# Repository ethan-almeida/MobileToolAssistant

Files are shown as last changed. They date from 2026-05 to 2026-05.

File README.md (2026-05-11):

# Mobile Tool Assistant

An autonomous mobile robot that follows a worker and carries tools in indoor industrial environments.

# Tools Used

## Hardware
- STM32F407DISCO Development Board
- ESP8266MOD Microcontroller (Remote node)
- 2x DWM1000 UWB Modules (User tracking)
- 3x VL53L1X ToF Sensors (Obstacle detection)
- L298N Motor Driver
- 2x TT DC Gear Motors
- Buck Converter Module
- Rechargeable AA NiMH Batteries (8x)
- BambuLab P1S 3D Printer (Chassis)
- Multimeter, Soldering Iron, Jumper Wires, Protoboard

## Software
- STM32CubeIDE v1.19.0
- Arduino IDE v2.3.7
- FreeRTOS (Real-time OS on STM32)
- Serial Debug Assistant
- GitHub (Version control)

## Repository Structure
```
MobileToolAssistant
├── DWM1000_tests/ # Iterative UWB development tests 
├── MobileToolAssistant/ # Final source code
│ ├── RemoteEnd/ # User remote node (ESP8266)
│ └── RobotEnd/ # Robot platform (STM32)
├── docs/ # Documentation and CAD files
└── README.md
```

## Quick Start

1. **Hardware setup**: See [User Manual](./docs/user_manual.pdf) for assembly, battery installation, and power-on steps.
2. **Build & flash**:
   - Robot: STM32CubeIDE project in `MobileToolAssistant/RobotEnd/`
   - Remote: Arduino IDE sketch in `MobileToolAssistant/RemoteEnd/`
3. **Operation**: Press the STANDBY button on the remote to start/stop following.

## Key Features

- UWB‑based user tracking (1m ± 0.5m following distance)
- ToF obstacle detection and avoidance
- Remote standby control
- Payload capacity: 1 kg
- Max following speed: 6 km/h

## Overall Block Diagram 
 

## Documentation

- [Requirements Specification](./docs/appendices/requirements_specification.pdf)
- [System Specification](./docs/appendices/system_specification.pdf)
- [Project Management](./docs/appendices/project_management.pdf)
- [User Manual](./docs/appendices/user_manual.pdf)
- [Final Report](./docs/final_report.pdf)

## Team

- Aneek Mohamed Ruksan
- Aditya Ramakrishnan
- Ethan D'Almeida
- Chidubem Emeka-Nwuba

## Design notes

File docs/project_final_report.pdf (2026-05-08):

DEPARTMENT OF ELECTRICAL AND COMPUTER ENGINEERING UNIVERSITY OF SASKATCHEWAN
ECE495-2025G5 | VERSION 1 | MOBILE TOOL ASSISTANT

© 2025 Chidubem Emeka-Nwuba, Aneek Mohamed Ruksan, Aditya Ramakrishnan, Ethan D’Almeida.
This document is CONFIDENTIAL and PROPRIETARY and is for the use of University of Saskatchewan personnel only, except to the extent that permission is expressly granted elsewhere.

In any event, no part of this document may be reproduced in any form without the express written consent of University of Saskatchewan.

UNIVERSITY OF SASKATCHEWAN. PROPRIETARY AND CONFIDENTIAL | Page 1 of 28
DOC NO: | ECE495-2025G5 | ISSUE DATE: | 07-04-2026
FILE NAME: | G5_assign7_final_report.pdf | VERSION NO: | 1
FILING PATH: | https://github.com/AneekMubarak/MobileToolAssistant/blob/main/docs/
TITLE: | Final Project Report
PROJECT: | Mobile Tool Assistant
KEYWORDS: | Report, schedule, objectives, constraints, testing

APPROVED BY

Daniel Teng | Date
Customer

PREPARED BY:

Aditya Ramakrishnan Date
Design Engineer

Aneek Mohamed Ruksan Date
Design Engineer

Chidubem Emeka-Nwuba Date
Design Engineer
Ethan D’Almeida | Date
Design Engineer

REVIEWED BY:

Chandler Janzen | Date
Supervisor

© 2025 Chidubem Emeka-Nwuba, Aneek Mohamed Ruksan, Aditya Ramakrishnan, Ethan D’Almeida.
This document is CONFIDENTIAL and PROPRIETARY and is for the use of University of Saskatchewan personnel only, except to the extent that permission is expressly granted elsewhere.

In any event, no part of this document may be reproduced in any form without the express written consent of University of Saskatchewan.

UNIVERSITY OF SASKATCHEWAN. PROPRIETARY AND CONFIDENTIAL | Page 2 of 28

REVISION HISTORY
Version No. | Date | Originator | Summary of Changes
1 | 29-03-2026 | E.D | Document created

## Table of Contents

## List of Tables

Table 1: Testing Setups and Results | 22
Table 2: Expected Project Schedule | 23
Table 3: Actual Project Schedule | 24
Table 4: Individual Member Contribution Summary | 25

## List of Figures

Figure 1: Final System Block Diagram | 9
Figure 2: Detailed Design - Motor Control Subsystem | 12
Figure 3:Detailed Design - Obstacle Detection Subsystem | 13
Figure 4: Detailed Design - User Detection: Robot Node | 21
Figure 5: Detailed Design - User Detection: Remote Node | 21
Figure 6: Gantt Chart for Expected and Actual Project Schedule | 24

## Executive Summary

This project presents the design and implementation of the Mobile Tool Assistant, a proof-of-concept robotic system developed to reduce the physical strain associated with transporting tools in industrial environments. Existing solutions such as carts and tool belts either require continuous manual effort or place excessive load on workers, creating safety and ergonomic concerns.
To address this problem, our team developed an autonomous, user-following robot capable of carrying tools while navigating indoor environments. The system integrates Ultra-Wideband (UWB) technology for accurate user tracking and Time-of-Flight (ToF) sensors for real-time obstacle detection and avoidance. A central STM32 microcontroller coordinates all subsystems, including motion control, navigation, and power management, enabling reliable and responsive operation. The prototype successfully demonstrates key functionalities, including maintaining a safe following distance, navigating around obstacles, and supporting remote user control. Testing results show consistent performance in tracking users at walking speeds and avoiding collisions, though payload capacity and motor performance were identified as limiting factors.
Despite challenges such as UWB calibration complexity and system integration delays, the project achieved its primary objective of delivering a functional and cost-effective mobile assistant. The modular design allows for future improvements, including enhanced sensing coverage, more robust hardware integration, and upgraded power systems.
Overall, this work demonstrates the feasibility of an affordable robotic assistant that can improve workplace safety, reduce fatigue, and enhance productivity in demanding environments.

## Statement of Work

### Problem Description

The project addresses the physical strain of manually transporting tools and equipment in harsh work environments where affordable and accessible transport systems are lacking. The goal is to develop a mobile robotic assistant that can detect a worker, map a route, and follow them to carry tools safely and cost-effectively.

### Problem Background

Most workers who work in demanding or harsh environments, i.e. industries or factories, often must carry heavy tools on their person. This becomes an issue especially in industrial environments where operators cannot afford to have excess weight on them, causing safety hazards.
While current methods attempt to address this challenge, they fall short in practice. Workers often rely on push carts, dollies, hand trolleys, and rolling toolboxes to move heavy equipment. These require constant pushing or pulling and can be difficult to maneuver on uneven surfaces or in tight spaces. Other solutions include using a portable tool belt or backpacks. These keep tools within reach but place the full weight directly on the worker’s body, increasing fatigue and risk of injury over long shifts.
This forms a need to make a mobile, autonomous, and tool-carrying system that can follow a worker, transport equipment safely, and reduce physical strain without requiring continuous manual operation.

### Scope

The project will demonstrate a working proof-of-concept of a mobile tool assistant. The team will design, build, and test a small-scale robotic platform that can autonomously follow a single worker and carry a payload of tools across a flat or moderately uneven indoor surface. The work will involve selecting and assembling appropriate hardware such as motors, sensors, a supporting frame, and a battery to create a safe and stable prototype. On the software side, the team will implement core functions such as person-tracking, obstacle avoidance so that the robot can reliably follow a worker in a controlled environment. A user remote will also be developed to allow a worker to toggle between following and standby modes of the robot without requiring constant supervision.

### Objectives

The project team shall:
1. Develop and deliver proof of concept of a mobile prototype of a compact and safe robot capable of transporting small tool loads in an indoor industrial environment.
2. Implement a reliable person-following capability that allows the robot to detect and follow a designated worker after activation.
3. Integrate obstacle detection and avoidance to minimize collision risk in a dynamic workspace.

4. Demonstrate usability and safety by producing a working prototype within one academic year and within the approved budget.

### Constraints

The following constraints shall limit the design and implementation:

1. Single-Floor Navigation: The system shall be restricted to operation on flat, single-level surfaces with little to no debris. The design shall not support stair climbing or traversal of steep inclines.
2. Indoor Use: The system shall be designed for operation in indoor environments only. Outdoor operation is excluded due to environmental complexity and weatherproofing requirements.
3. Payload Capacity: The system shall be capable of carrying a moderate tool payload only, as limited by motor performance, chassis strength, and available project resources.
4. Timeframe: The project shall be executed within the academic year, which constrains the scope to the development of core functionalities rather than advanced features.
5. Team Size: The project shall be executed by a team of four members. The limited manpower constrains the project scope, task allocation, and development capacity within the given timeframe.
6. Budget: The project shall operate under limited financial resources, restricting the use of high-cost sensors, materials, and hardware.

### Key Considerations

The robotic assistant shall operate safely and non-distractingly, maintaining an appropriate distance from workers and functioning predictably to avoid interfering with normal workflows. The design should incorporate reliable load management, robust battery management, and durable, energy-efficient components to meet safety and operational requirements. The project should also emphasize positive social impact by reducing physical strain on workers, ensuring ease of use and accessibility, and reinforcing the role of the robot as an assistant that supports productivity rather than replacing human labor.

## Final System Block Diagram

The final system architecture of the Mobile Tool Assistant is designed as a modular, real-time embedded system that integrates user tracking, obstacle detection, motion control, and power management into a cohesive autonomous platform. The system enables the robot to follow a designated user while safely navigating indoor environments.

At a high level, the system consists of six primary subsystems: User Tracking, Navigation (Obstacle Detection), Motion Control, Processing and Communication, Power Management, and User Interface, all coordinated by a central microcontroller.

The User Tracking subsystem utilizes Ultra-Wideband (UWB) technology to estimate the relative position of the user. Two UWB anchors mounted on the robot perform ranging with a remote UWB node carried by the user. Using these distance measurements, the system computes the user’s position and heading relative to the robot.

The Navigation subsystem consists of multiple Time-of-Flight (ToF) sensors that continuously monitor the environment for obstacles. These sensors provide distance measurements that are used to detect potential collisions and trigger avoidance maneuvers.

The Motion Control subsystem translates tracking and navigation data into motor commands. It implements control logic to maintain a safe following distance while dynamically adjusting speed and direction. Obstacle avoidance is handled using a state-machine-based approach to ensure predictable and stable behavior.

The Processing and Communication subsystem is implemented on an STM32 microcontroller and acts as the core of the system. It handles sensor data acquisition, UWB communication, decision-making, and coordination between subsystems in real time.

The Power Management subsystem distributes power from a single battery source to all components. It includes voltage regulation for logic-level electronics and direct supply for motors, ensuring stable and efficient operation.

Finally, the User Interface subsystem allows the user to interact with the robot through a remote node and onboard controls. It enables start/stop functionality and provides basic system feedback.

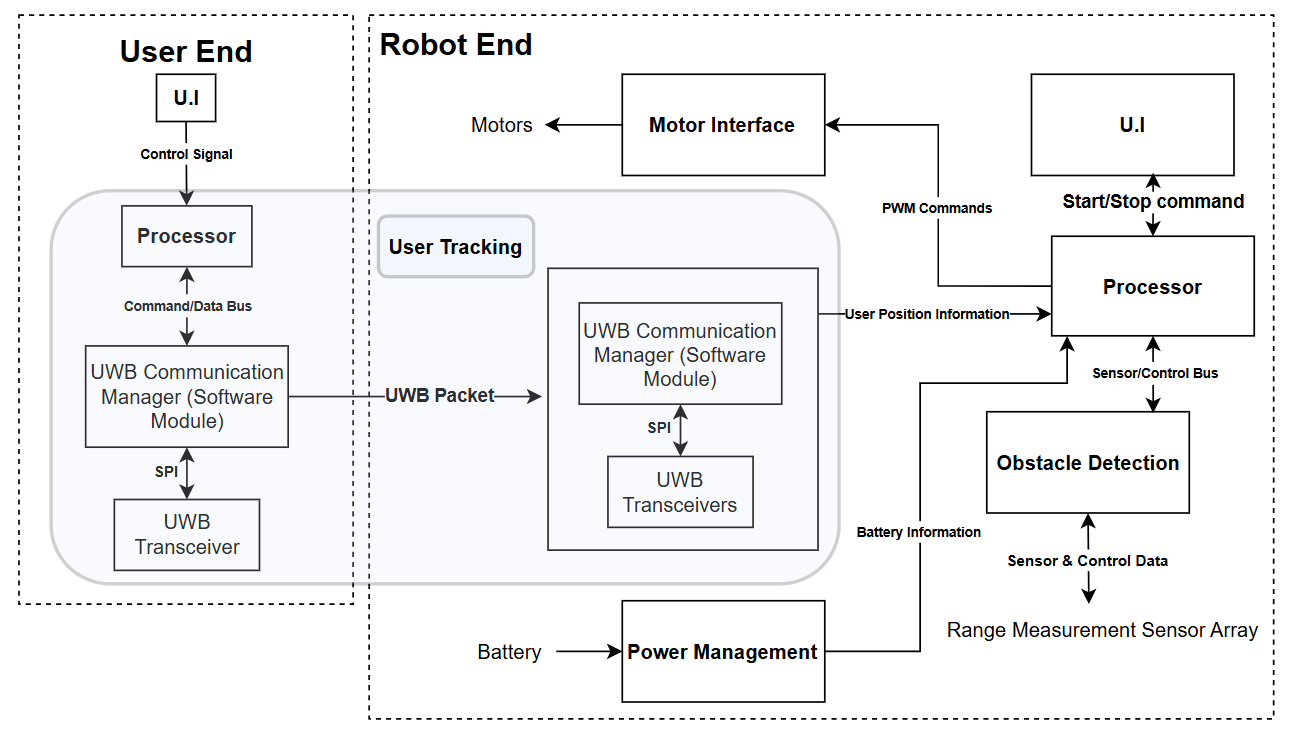
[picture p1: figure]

Figure 1: Final System Block Diagram

### System Alternatives and Design Selection

Several system architectures were considered during the design phase, including:
- Vision-based tracking with LiDAR navigation
- BLE-based tracking with RSSI and stereo vision
- BLE with IMU-assisted tracking
- UWB-based tracking (final design)
Each alternative was evaluated based on cost, complexity, power consumption, reliability, and implementation feasibility. Vision-based systems offered high accuracy but were computationally expensive and sensitive to lighting conditions. BLE-based approaches were low-cost but suffered from poor positional accuracy due to signal variability.
The UWB-based system was selected as the final design because it provides high-accuracy distance measurements, low latency, and robustness in indoor environments, while remaining within project cost and power constraints. This made it the most balanced and practical solution for a real-time following system.

### Key Design Decisions

Several important design decisions were made to ensure system performance and feasibility:
- Use of dual UWB anchors: Enabled triangulation of user position rather than relying on a single distance measurement, improving tracking accuracy.
- RTOS-based control architecture: Simplified implementation of all subsystems and ensured predictable system behavior.

- Modular subsystem design: Allowed independent development and testing of tracking, control, and sensing components.
- Use of ToF sensors over LiDAR: Reduced system cost and power consumption while still meeting obstacle detection requirements.
- Single battery power architecture: Simplified integration and reduced hardware complexity.

### Design Challenges and Solutions

Several challenges were encountered during system development:
- UWB calibration and instability:
Achieving accurate distance measurements required careful calibration of antenna delays and filtering of noisy readings. This was addressed through averaging multiple samples and iterative calibration.
- Integration of multiple subsystems:
Synchronizing tracking, obstacle detection, and motion control introduced timing and communication challenges. These were mitigated by implementing structured state machines and prioritizing obstacle avoidance over tracking.
- Limited field of view for tracking:
The use of two front-mounted UWB anchors restricted tracking to a forward-facing region. This limitation was accepted for the prototype but identified for future improvement.
- Motor performance under load:
The robot experienced reduced performance with higher payloads. This was partially mitigated through speed control adjustments and is noted as a limitation of the prototype hardware.

## Final Detailed Design

(A – Aditya Ramakrishnan, B – Aneek Mohamed Ruksan, C –Chidubem Emeka-Nwuba, D – Ethan Peter D’Almeida)

### Processor (A: 90% C: 10%)

Purpose:
The Processor Module reads all sensor inputs, determines the robot’s motion commands, and sends control signals to the motor drivers. It handles UWB ranging, battery monitoring, state decisions, and safety shutdown actions at the robot’s end.
Inputs:
- UWB Positional Data & Start/Hold Commands
- ToF Sensor Obstacle Detection Distance Data array
- Battery Voltage/Current
Outputs:
- 4× PWM Motor Signals
- UWB Configuration Commands

Parts Required:
- STM32F407DISC0 Development Board
- STM32CubeIDE

### Motor Control (D: 100%)

Purpose:
The motion control subsystem is responsible for converting the user’s position from the User Tracking subsystem into motor drive signals.
Inputs:
- User Position (x, y) from User Tracking subsystem.
- System State (from obstacle detector and from UI) Parts Required:
- 2x TT Gear Motor
- 1x L298N Driver
Algorithm:
- Read raw ToF distances from the left, center, and right sensors.
- If in “STANDBY_MODE”, immediately stop motors and reset the obstacle state machine.
- Obstacle avoidance is handled by a 3-phase state machine
- The states are: - OBST_STATE_STOP_BEFORE, OBST_STATE_ACTION, OBST_STATE_STOP_AFTER
- Motor Control Logic:
- If center < OBSTACLE_THRESHOLD_CLOSE, then the reverse command is given, dodgeAngle is set to 180 degrees, and the state machine is initiated.
- If center_blocked is true, then the robot will turn towards the side with more clearance, i.e., turn left by 135 degrees and turn right by 45 degrees.
- If left_blocked then turn right at 45 degrees.
- If right_blocked then turn left at 135 degrees.
- If both sides are blocked but the center is clear, move forward at constant speed and maintain a dodgeAngle of 90 degrees.
- UWB Following Logic:
- If the distance from the remote to the robot is within the range of 0.25 m to 30 m, the angle is within a range of 0 to 180 degrees, and the valid flag is set, then the UWB data will be accepted.
- The robot will stop if the distance to the remote is less than or equal to 100 cm and will only resume when that distance becomes greater than 115 cm (tolerance measure).
- Speed Control Logic:

- The PWM signal is adjusted by the distance from the remote to the robot, i.e., a smaller distance results in a lower speed, and a higher distance results in a higher speed.

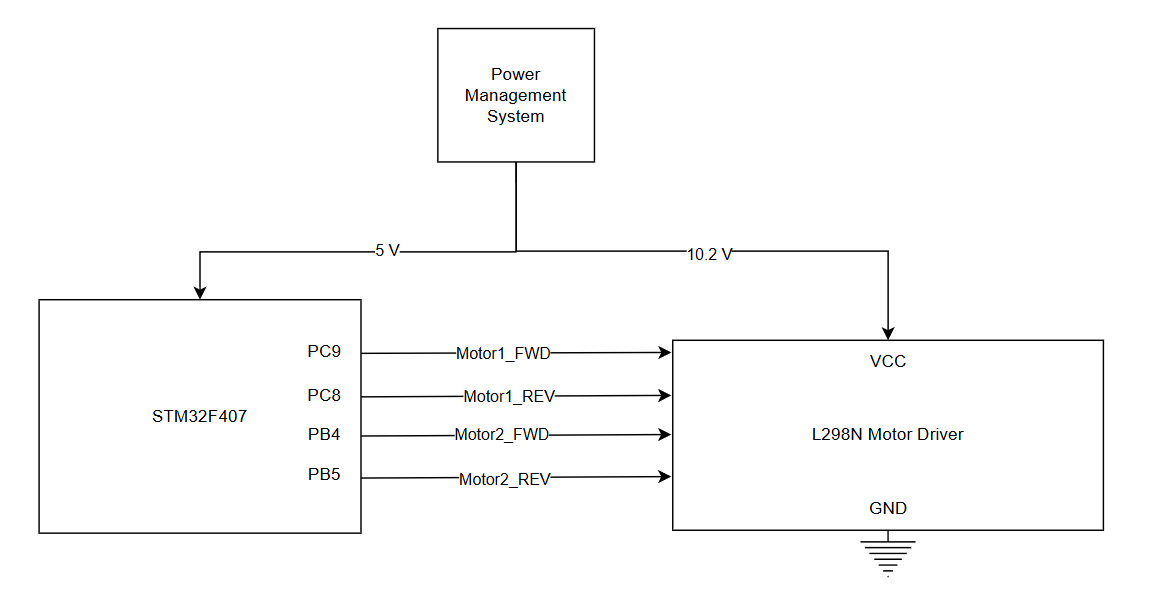
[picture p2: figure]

Figure 2: Detailed Design - Motor Control Subsystem

### Obstacle Detection (C: 90%, A: 10%)

Purpose:
The purpose of the Obstacle Detection subsystem is to detect obstacles in the robot’s path from a minimum distance of 1.5m. This information is then sent to the microcontroller to process and make decisions on whether to keep following the user or avoid an incoming obstacle. The decision is made based on the sensor data stored in a data array for each sensor. The sensors used are 3 VL53L1X placed to provide coverage to the front-facing side of the robot (Refer to Figure 3 for wiring/connection specifications).
Outputs:
Obstacle detection distances from each ToF sensor
Software Algorithm:
- Monitors surroundings using left, center, and right ToF sensors with filtered distance readings
- Determines whether paths are blocked based on distance thresholds (center and side zones)
- Prioritizes obstacle avoidance over normal movement and pauses user-following when needed

- Executes avoidance maneuvers through a state machine to complete multi-step actions reliably
- Reverses immediately when an obstacle is detected very close in front
- Chooses a turn direction (left or right) based on which side has more clearance
- Turns away from obstacles detected on only one side
- Continue moving forward when only side paths are blocked, but the center is clear
- Adjusts its dodge angle to guide the direction of avoidance maneuvers
- Resumes normal user-following behavior when no obstacles are detected

Parts Required:
1. 3 VL53L1X sensors
2. Protoboard to solder buses together
3. Jumper wires (to connect to MCU)

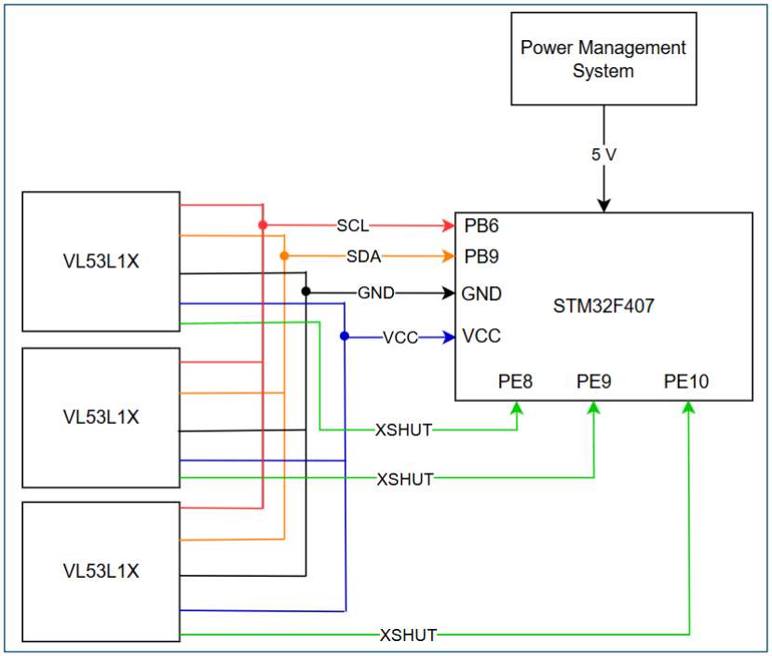
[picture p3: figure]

Figure 3:Detailed Design - Obstacle Detection Subsystem

### Power Management (A: 100%)

Purpose:
The Power Management Module provides the required voltage for the robot from an 8-cell rechargeable AA battery pack connected in series. The battery pack supplies power directly to the motor driver and feeds a buck converter that steps the voltage down to 5 V for the STM32F407 board. The board then powers and interfaces with UWB modules and distance sensors. This allows the robot to use a single battery source for both motor actuation and control electronics.

Output:
- Approximately 9.6 V nominal battery supply to motor driver
- Approximately 10.2 V when fully charged at startup
- 5 V rail to STM32F407 board through buck converter
- Power to 2× UWB modules through the board
- Power to 3× distance sensors through the board

Parts Required:
- 8 × Energizer rechargeable NiMH AA batteries (1.2 V each)
- 1 × battery holder/connector
- 1 × motor driver
- 1 × buck converter
- 1 × STM32F407 board
- 2 × UWB modules
- 3 × distance sensors
- 2 × yellow DC motors

Power setup:
- Connect the 8 AA rechargeable batteries in series to create the main supply voltage.
- Provide this battery voltage directly to the motor driver to power the motors.
- Feed the same battery voltage into the buck converter.
- Step the battery voltage down to a regulated 5 V output.
- Supply the 5 V output to the STM32F407 board.
- Use the STM32F407 board to power and interface with UWB modules and distance sensors.
- Continue operation while the battery pack provides supicient voltage.

Power Calculation:

Battery Pack Voltage
Nominal Voltage (V) = 8 ∗ 1.2V = 9.6V Fully charged (measured):
V ≈ 10.2 V
Motor Power (2 DC Yellow Motors) = ~10 V / ~0.25 A eacℎ (under load)

Rated electrical power per motor: P = 10 V × 0.25 A = 2.5 W

Total motor power:
P_total = 2 × 2.5 W = 5.0 W STM32F407 Development Board Power − 5 V / ~0.15 A P = 5 V × 0.15 A = 0.75 W
UWB Modules (2 × DWM1000) − 3.3 V / ~0.16 A eacℎ

Total current:
I = 2 × 0.16 A = 0.32 A

Total UWB power:
P = 3.3 V × 0.32 A = 1.056 W Distance Sensors (3 × ToF) − 5 V / ~0.02 A eacℎ

Total current:
I = 3 × 0.02 A = 0.06 A

Total sensor power:
P = 5 V × 0.06 A = 0.30 W

Total Average Power:
P_total = 5.0 W + 0.75 W + 1.056 W + 0.30 W P_total = 7.106 W

### User Tracking (B:100%)

Purpose:
The User Tracking subsystem determines the position of the user relative to the front of the robot so that the motion controller can steer toward the user and maintain the desired following distance. The implemented design uses two front-mounted UWB anchors on the robot and one UWB transceiver on the remote carried by the user. Distances from the left and right robot anchors to the remote are measured using Double-Sided Two-Way Ranging (DS-TWR), then converted into user position, distance, and heading angle.

Physical Setup:
The robot node uses two DWM1000 UWB modules mounted at the front of the robot on a rigid horizontal arm. The modules are placed 30 cm apart, centered about the robot midpoint, so that the left anchor is at −15 cm and the right anchor is at +15 cm relative to the robot centerline. This baseline is used directly in the triangulation calculation. The arm is mounted parallel to the front edge of the robot chassis so that both modules face forward and remain fixed relative to one another. The robot-side processing runs on the STM32F407 board as part of the RTOS application. The remote node carried by the user contains one DWM1000 module, one ESP8266MOD, and one pushbutton. The push button is used to transmit a standby control message to the robot. On the robot side, receipt of this message toggles the standby state used by the rest of the system. Inputs:
- UWB ranging frames received from the remote node
- Standby command embedded in remote UWB communication
Outputs:
- User position relative to robot center, (x, y), in cm
- User distance from robot center in cm
- User heading angle in degrees
- Standby state flag for higher-level control logic

Parts Required:
Robot Node:
1. STM32F407 development board
2. 2 x DWM1000 UWB Modules
3. 1 x rigid front mounting arm for the anchors (30cm)
4. Wiring for SPI, reset, interrupt and power connections

Remote Node:
1. ESP8266MOD Microcontroller
2. 1 x DWM1000 Module
3. 1 x Pushbutton for standby control
4. Portable power source for the remote node (5V).

System Operation:
The robot does not estimate position from a single UWB reading. Instead, it ranges separately to the left and right front anchors and then computes the user’s position geometrically. For each anchor, the ranging exchange is performed using DS-TWR. In one ranging cycle, the robot sends a Poll frame, the remote replies with a Response frame, the robot sends a second Poll 2 frame, and the remote replies with a Final frame. Timestamps recorded on both sides are used to compute the signal propagation time while compensating for reply delays. The propagation time is converted to distance, corrected using antenna-delay compensation.

The DS-TWR propagation time is calculated as: t!"#! = (rtt$. rtt%) − (reply$. reply%) rtt$ + rtt% + reply$ + reply% Where:
- t!"#!: Signal propagation time between the robot and the remote node
- rtt$: Round-trip time measured during the first message exchange (Poll to Response)
- rtt%: Round-trip time measured during the second message exchange (Poll2 to Final)
- reply$: Reply delay at the remote node (time between receiving Poll and sending Response)
- reply%: Reply delay at the robot (time between receiving Response and sending Poll 2)

The measured distance (d) is then computed from:
d = t!"#!. c
Where c is the speed of light. In the implementation, antenna delay is subtracted before the time is converted to distance.
To reduce noise, the robot averages multiple distance measurements from the left and right anchors before computing the user position. The code uses an averaging count of 5 samples. After valid left and right distances are available, the position is calculated using the fixed baseline between the anchors
Coordinate System:
The coordinate system is defined with the robot center at the origin. Positive x points to the robot’s right side, and positive y points forward. With the anchor baseline B = 30cm, the left anchor is located at (−15,0)and the right anchor is located at (+15,0). The user position is calculated from the left and right distances d&and d'as:
x = d&

% − d'

%
2B
y = ](d&
% − ^x +

B
2

_

%

The user's distance from the robot center is then: d = `x% + y%
The user heading angle is computed from:
θ = atan2(y, x)
In this convention, 0° is directly to the right of the robot, 90° is straight ahead, and 180° is directly to the left.
Standby Control:
The remote node also transmits a control message used to toggle standby mode. On the robot side, if the received message type is identified as a standby frame, the standby flag is toggled. This allows the user to command the robot to pause or resume tracking using the push button on the remote.
UWB Configuration Parameters:
The DWM1000 modules on both the robot and remote nodes are configured using a fixed set of communication parameters to ensure consistent ranging performance. The following configuration is used for all UWB devices in the system:
- Channel: 5
- Pulse Repetition Frequency (PRF): 16 MHz
- Data Rate: 6.8 Mbps
- Preamble Length: 1024 symbols
- PAC Size: 32
- SFD: Standard
- Antenna Delay: Calibrated per module
Channel 5 and a data rate of 6.8 Mbps were selected to achieve reliable communication with low latency and sufficient range (~30 m) for the intended indoor tracking environment.
All nodes must use identical configuration parameters to ensure successful communication and accurate ranging.
SPI Communication Configuration:
The SPI interface used to communicate with the DWM1000 modules is initialized at a lower clock frequency during startup and configuration, then increased for normal operation. Initialization Phase SPI Speed: Remote node - 3 MHz; Robot node - 328.125 kHz
Operational Phase SPI Speed: Remote node - 20 MHz; Robot node - 10.5 MHz
UWB Message Structure:
To distinguish between different stages of the DS-TWR protocol and control messages, a custom message format is used for all UWB transmissions.

Each transmitted frame contains a fixed 6-byte payload. The most significant byte (MSB) of the payload represents the message type, while the remaining 5 bytes (lower 40 bits) are used to store timing-related values such as timestamps or reply delays required for DS-TWR calculations.

The following message types are defined:
- 0xA1 – POLL
- 0xB2 – RESPONSE
- 0xA2 – POLL_2
- 0xA3 – FINAL
- 0x69 – STANDBY CONTROL
During operation, the receiving node inspects the message type field to determine the appropriate state transition and processing logic.

In addition to the message type, RESPONSE and FINAL frames include embedded timing information required for DS-TWR calculations, such as reply delays and timestamps.

This structured message format ensures correct synchronization between the robot and remote nodes and enables reliable execution of the ranging protocol and standby control.
Algorithm:
The User Tracking subsystem is implemented using finite state machines on both the robot node and the remote node. The robot state machine manages the DS-TWR ranging process and distance computation, while the remote state machine handles message responses and control transmission. Each state represents a specific stage in the ranging protocol, ensuring reliable communication, timing control, and error recovery.
Robot State Machine States:
- RSTATE_SEND_POLL
- RSTATE_WAIT_RESPONSE_1
- RSTATE_SEND_POLL_2
- RSTATE_WAIT_RESPONSE_2
- RSTATE_COMPUTE
- RSTATE_ERROR_RECOVERY

Remote State Machine States:
- REMOTE_WAIT_M1
- REMOTE_SEND_M2
- REMOTE_WAIT_TX_DONE
- REMOTE_WAIT_M3
- REMOTE_SEND_M4
- REMOTE_WAIT_TX_DONE_FINAL

The following algorithm describes the real-time execution of the state machines on both robot and remote nodes.
1. Initialize SPI, reset, and interrupt interfaces and apply the predefined UWB configuration parameters.
2. Set the robot ranging state to RSTATE_SEND_POLL for the active anchor and set the remote state to REMOTE_WAIT_M1.
3. For the active robot anchor, transmit a POLL frame to the remote node.
4. On the remote node, wait in REMOTE_WAIT_M1 until a valid POLL frame is received. If the received frame is invalid or a timeout occurs, clear status flags, reset the remote session, and return to REMOTE_WAIT_M1.
5. After receiving a valid POLL frame, the remote records the reception timestamp, computes the reply delay, and enters REMOTE_SEND_M2. It then transmits a delayed RESPONSE frame containing the reply timing information and moves to REMOTE_WAIT_TX_DONE.
6. The robot waits in RSTATE_WAIT_RESPONSE_1 for the Response frame. If the frame is invalid or a timeout occurs, the robot enters RSTATE_ERROR_RECOVERY, clears the transceiver state, and restarts the ranging sequence for that anchor.
7. After a valid RESPONSE frame is received, the robot stores the received timing data, transmits a second POLL_2 frame, and enters RSTATE_WAIT_RESPONSE_2.

8. On the remote node, once transmission of the RESPONSE frame is complete, the state machine moves to REMOTE_WAIT_M3. The remote waits for a valid POLL_2 frame. If reception fails or the wrong message type is received, the remote resets its session and returns to REMOTE_WAIT_M1.
9. After receiving POLL_2, the remote records the second reception timestamp, computes the second delayed reply, enters REMOTE_SEND_M4, and transmits the FINAL frame. It then waits in REMOTE_WAIT_TX_DONE_FINAL and, after successful transmission, returns to REMOTE_WAIT_M1.
10. The robot receives the FINAL frame in RSTATE_WAIT_RESPONSE_2. Using the stored timestamps and reply values, it computes the DS-TWR propagation time, applies antenna-delay compensation, and converts the result to distance for the active anchor. It then enters RSTATE_COMPUTE.
11. If the computed distance is valid, store it in the averaging buper for that anchor. If the measurement is invalid, discard it and restart the ranging sequence.
12. Repeat the ranging process for both left and right anchors to obtain one valid distance measurement from each.
13. Continue collecting measurements until the required number of valid samples is reached for both anchors. Average the left and right distances using the configured sample count of 5 to reduce noise before position estimation.
14. Use the averaged left and right distances to compute the user position (x, y), total distance from the robot center, and heading angle relative to the front of the robot.
15. Check the received message type for a standby control message. If a standby frame is detected, toggle the standby flag so the robot pauses.
16. Output the updated user position, distance, angle, and standby state to be used by the motion control subsystem.
17. Repeat the full process continuously while the system is powered.

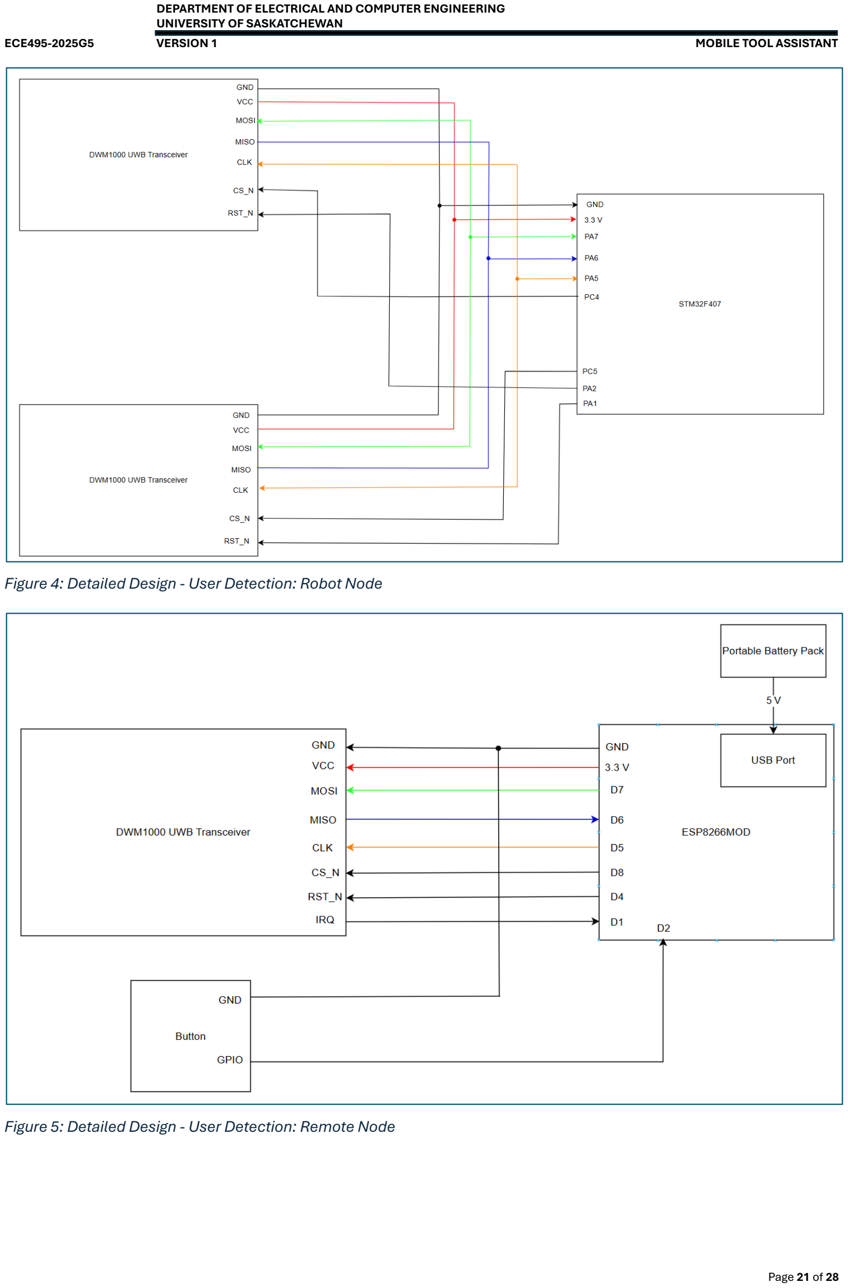
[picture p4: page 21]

Figure 4: Detailed Design - User Detection: Robot Node

Figure 5: Detailed Design - User Detection: Remote Node

## Development Environment

1. Hardware Used: -
- Multimeter
- Soldering Iron
- BambuLab P1S 3D printer
2. Software Used: -
- STM32Cube IDE v1.19.0
- Serial Debug Assistant
- Arduino IDE v2.3.7

## Testing Setups and Results

Table 1: Testing Setups and Results

Test ID | Requirement | Test Objective | Test Procedure | Expected Result | Actual Result
T1 | Follow distance: 1m ± 0.5 | Verify the robot maintains a proper following distance from the remote. | Place the robot at varying distances (0.5m to 2m) and measure the actual following distance | The robot should be able to maintain an average distance of 1m, ± 0.5m in all trials. | Robot maintains an average following distance of 1 ± 0.5 m in all the trials we conducted.
T2 | Follow speed: 5 km/h, ±1 km/h | Verify the robot’s ability to follow a moving user at a specified speed. | The user should move at speeds up to 5 km/h to measure the robot's following feature. | The robot should be able to track and follow a user in the environment it is operating in. | The robot was successfully able to track and follow the user at walking speeds of up to 6 km/h.
T3 | Payload: 5 kg capacity | Verify the robot’s ability to carry a payload safely. | Place a payload on the robot that weighs up to 5 kg and checks if it can follow the user in its operating environment. | The robot should be able to track and follow a user with a payload of up to 5kg in weight. | The robot was able to track and follow a user with a payload of up to 1kg without any issues. An increase in weight resulted in significant speed drops due to motor constraints.

T4 | Obstacle Detection

Verify the
robot’s ability
to detect and
avoid
obstacles.

Place static
obstacles
within 50 cm of
the robot’s
path.

The robot
should be able
to detect
obstacles
within 50 cm of
it and adjust its
path to
continue
tracking and
following the
user.

The robot was
able to
successfully
detect
obstacles
within 50 cm of
its path and
adjust its
course to
continue
following the
user.

## Actual v/s Expected Project Schedule

### Table 2: Expected Project Schedule

Task ID | Task Name | Estimated Hours | Responsible Member | Precedence | Expected Deadline
1 | Detailed Design (Assignment) | 20h | Chidubem | None | 27th Nov,2025.
2 | Parts Selection and Ordering | 10h | Aditya | T1 | 1st Dec,2025.
3 UWB Tracking Module (User | Tracking) | 40h | Aneek | T2 | 21st Jan, 2026.
4 | Obstacle Detection | 45h | Chidubem | T2 | 21st Jan, 2026.
5 Motion Control Algorithm (Motor | wiring) | 21h | Ethan | T3, T4 | 30th Jan, 2026
6 User Interface (and User Node | Assembly) | 20h | Aneek | T3 | 30th Jan, 2026
7 | Power Management System | 24h | Aditya | T1 | 21st Jan, 2026
8 System Assembly and Integration | (Constructing Prototype) | 30h | Chidubem | T5, T6, T7 | 15th Feb, 2026
9 Chassis Design and | Printing/Ordering | 15h | Aditya | T8 | 15th Feb, 2026
10 | System Testing and Debugging | 37h | Ethan | T9 | 28th Feb, 2026
11 System Refining and | Performance Improvement | 16h | Aneek | T10 | 28th Feb, 2026

### Table 3: Actual Project Schedule

Task ID | Task Name | Actual Hours Spent | Responsible Member | Precede nce | Completion Date
1 | Detailed Design (Assignment) | 20h | Chidubem | None | 27th Nov 2025.
2 | Parts Selection and Ordering | 25h | Aditya | T1 | 27th Jan 2026.
3 UWB Tracking Module (User | Tracking) | 175h | Aneek | T2 | 12th Mar 2026.
4 | Obstacle Detection | 45h | Chidubem | T2 | 4th Mar 2026.
5 Motion Control Algorithm (Motor | wiring) | 43h | Ethan | T3, T4 | 24th Mar 2026
6 User Interface and User Node | Assembly | 5h | Aneek | T3 | 13th Mar 2026
7 | Power Management System | 24h | Aditya | T1 | 20th Mar 2026
8 System Assembly and Integration | (Constructing Prototype) | 30h | Chidubem | T5, T6, T7 | 23rd Mar 2026
9 Chassis Design and | Printing/Ordering | 15h | Aditya | T8 | 19th Mar 2026
10 | System Testing and Debugging | 40h | Ethan | T9 | 24th Mar 2026
11 System Refining and | Performance Improvement | 37h | Aneek | T10 | 24th Mar 2026

Figure 6: Gantt Chart for Expected and Actual Project Schedule

Planned
Actual

Expected vs Actual Project Schedule

Legend

Task | November | December | January | February | March

Detailed Design

Part Selection and Ordering

UWB Tracking Module/User Tracking

Obstacle Detection

Motion Control Algorithm

User Interface (and User Node Assembly) !D#$%&'()(*$+$),&-./,$+

-./,$+&0//$+12.&()3&4),$*%(,5D)&67D)/,%89,5)*&!%D,D,.:$; 7<(//5/&=$/5*)&()3&!%5),5)*

-./,$+&>$/,5)*&()3&=$18**5)*&

-./,$+&?$@5)5)*&()3&!$%@D%+()9$&4+:%DA$+$),

### Table 4: Individual Member Contribution Summary

Member | Total Hours | Key Contributions
Aneek Mohamed Ruksan | 180 | UWB User Tracking, UI/User Node
Aditya Ramakrishnan | 120 | Motor Control Algorithm, Power Management System, Obstacle Avoidance, Chassis Design and Printing, System Refining and Improvement, System Assembly
Ethan D’Almeida | 70 | UWB calibration support and testing, documentation, obstacle detection, and avoidance improvements
Chidubem Emeka-Nwuba | 75 | Obstacle Detection Subsystem Assembly and Integration, Software architecture: implementation, management, and subsystem task integration

Project Analysis and Reflection
The project did not follow the original schedule mainly because some tasks were much more difficult than expected. The biggest issue was our lack of experience with UWB technology, which led to large delays early on the project and later affected many tasks. The largest difference was in the UWB tracking module (Task-3), which took us 175 hrs to complete and get fully working rather than the planned 40 hrs. Main challenges in this task that can be attributed to the delay include: -
- Calibrating the antenna delay, which required multiple rounds of testing and adjustments.
- Implementing the double-sided two-way ranging algorithm correctly.
- Fixing drift in tracking and unstable position and direction readings.

This task was required because it was the highlight feature of our project and had to be completed before others could start, which caused a chain reaction that pushed back multiple tasks, such as motion control and system integration.

Other tasks also took longer than expected, such as: -
- Parts Selection (Task-2): Took 25 hrs instead of 10 hrs due to re-designs and part availability.
- Motion Control (Task-5): Took 43 hrs instead of 21 hrs due to issues in integration.
- System Refinement (Task-11): Took 37 hrs instead of 16 hrs due to extra testing and improvements, specifically in the obstacle avoidance algorithm.
However, some time was saved in the User Interface (Task-6), which only took 5 hrs instead of 20 hrs because the design was simplified.

Mitigation Strategies

To deal with the delays, our team made some adjustments: -
- Ethan helped Aneek with UWB calibration and testing, which improved progress on one of the more dipicult tasks in the project.
- Some tasks, such as obstacle detection and the power management system, were done in parallel to reduce any further delays.
- Features like the user interface were greatly simplified to save time.
- Instead of waiting till the end, we tested parts of the system to catch any problems earlier.
- More time was spent on testing and refinement to ensure the system worked reliably.

## Recommendations

While the final system meets the core project requirements, it was developed as a proof-of-concept prototype with several design trade-offs that impact performance, reliability, and scalability. One key limitation was in the UWB tracking system, where the use of only two sensors provided a 180° field of view, constraining the user to remain in front of the robot; in the intended design, adding a third sensor at the rear would enable full 360° coverage and allow continuous tracking regardless of user position. Similarly, the prototype relied primarily on ToF sensors for obstacle detection, which limited environmental awareness; integrating a 360° LIDAR sensor in the final design would provide comprehensive planar coverage for navigation, while the existing ToF sensors could be retained for vertical distance measurement, resulting in improved obstacle detection and avoidance across a wider range of scenarios. Additionally, the use of jumper wire connections in the prototype, while beneficial for rapid development, introduced reliability issues such as loose connections, signal instability, and inconsistent test results; transitioning to custom PCBs in the intended design would significantly enhance electrical reliability, mechanical robustness, and signal integrity, while also simplifying assembly, reducing noise susceptibility, and enabling more accurate and repeatable system testing. Finally, future iterations will focus on improving the power system by transitioning to an industry-standard lithium-ion battery module, like those used in robotic vacuum platforms such as Roomba; this would involve a sealed, rechargeable battery pack with an integrated battery management system, enabling safer operation, higher energy density, and more reliable long-term performance.

## Conclusions

Our project successfully developed and tested a mobile robotic assistant, demonstrating a cost-effective solution for transporting heavy tools in demanding industrial environments. Our design integrates Ultra-Wideband (UWB) and Time-of-Flight (ToF) sensor technologies, providing a robust platform capable of autonomously tracking a worker while maintaining safe distances and navigating around dynamic obstacles. Furthermore, our implementation of a remote-based standby control system ensures the robot operates as an intuitive assistant that responds to user commands without requiring constant manual supervision.
The design relies on a modular architecture, utilizing a central STM32 microcontroller to process UWB ranging data and ToF obstacle inputs, which are then translated into precise motor commands. The UWB modules allow for reliable user localization via trilateration, while the ToF sensor array provides real-time environmental awareness, enabling the robot to navigate safely in tight, indoor workspaces. These components allowed our team to implement a functional proof-of-concept using a budget-conscious approach that prioritizes both safety and ease of use.
While further refinement is necessary, specifically regarding long-term signal stability and power system optimization, the prototype successfully proves the core concepts of autonomous person-following and obstacle avoidance. The development process has provided a clear roadmap for future iterations, including moving to custom PCB designs and higher-density battery solutions. Ultimately, this work contributes to the development of affordable, high-utility robotic assistants designed to reduce physical strain and increase productivity for workers in industrial and construction settings.

## References

Decawave Ltd. (2017). DW1000 product datasheet (Version 2.22) [Data sheet]. https://www.qorvo.com/products/p/DW1000

Decawave Ltd. (2017). DW1000 user manual (Version 2.18) [User manual]. https://www.qorvo.com/products/p/DW1000

Qorvo. (n.d.). DWM1000 ultra-wideband module (Version 2.0) [Data sheet]. https://www.qorvo.com/products/d/da007948

Amazon Web Services, Inc. (2017). FreeRTOS reference manual (Version 10.0.0) [Reference manual].
https://www.freertos.org/media/2018/FreeRTOS_Reference_Manual_V10.0.0.pdf

STMicroelectronics. (2024). VL53L1X time-of-flight ranging sensor (Rev. 8) [Data sheet]. https://www.st.com/resource/en/datasheet/vl53l1x.pdf

STMicroelectronics. (2026). STM32F407xx Development Board (Rev. 11) [Data sheet]. https://www.st.com/resource/en/datasheet/dm00037051.pdf

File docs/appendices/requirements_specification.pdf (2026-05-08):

DEPARTMENT OF ELECTRICAL AND COMPUTER ENGINEERING UNIVERSITY OF SASKATCHEWAN
ECE495-2025G502 | VERSION 0.2 | REQUIREMENT SPECIFICATION

© Chidubem Emeka-Nwuba, Aneek Mohamed Ruksan, Aditya Ramakrishnan, Ethan D’Almeida.

This document is CONFIDENTIAL and PROPRIETARY and is for the use of the copyright holders, except to the extent that permission is expressly granted elsewhere.

In any event, no part of this document may be reproduced in any form without the express written consent of the copyright holders.

UNIVERSITY OF SASKATCHEWAN. PROPRIETARY AND CONDIDENTIAL | Page 1 of 9
DOC NO: | ECE495-2025G502 | ISSUE DATE: | 07-10-2025
FILE NAME: | g5_assign2_requirements_specification.pdfVERSION NO: | 0.2
FILING PATH: | https://github.com/AneekMubarak/MobileToolAssistant/blob/main/docs/
TITLE: | Requirement Specification
PROJECT: | Mobile Tool Assistant
KEYWORDS: | tools, assistant, navigation, transport, follow, requirements, specifications, constraints,
| functional, non-functional.

APPROVED BY

Daniel Teng | Date
Customer

PREPARED BY:

Chidubem Emeka-Nwuba | Date
Design Engineer
Aditya Ramakrishnan | Date
Design Engineer
Aneek Mohamed Ruksan | Date
Design Engineer
Ethan D’Almeida | Date
Design Engineer

REVIEWED BY:

Chandler Janzen | Date
Supervisor

© Chidubem Emeka-Nwuba, Aneek Mohamed Ruksan, Aditya Ramakrishnan, Ethan D’Almeida.

This document is CONFIDENTIAL and PROPRIETARY and is for the use of the copyright holders, except to the extent that permission is expressly granted elsewhere.

In any event, no part of this document may be reproduced in any form without the express written consent of the copyright holders.

UNIVERSITY OF SASKATCHEWAN. PROPRIETARY AND CONDIDENTIAL | Page 2 of 9

REVISION HISTORY
Version No. | Date | Originator | Summary of Changes
1 | 07-10-2025 | C.E.N, A.R, E.D, A.M.R | Document Created
2 | 04-11-2024 | E.D | Modified Design Constraints, reframed some requirements
3 | 25-03-2026 | E.D | Updated Design Constraints, updated detection thresholds
4 | 07-04-2026 | C.E.N, A.R | Updated requirements, constraints and key requirements

© Chidubem Emeka-Nwuba, Aneek Mohamed Ruksan, Aditya Ramakrishnan, Ethan D’Almeida.

This document is CONFIDENTIAL and PROPRIETARY and is for the use of the copyright holders, except to the extent that permission is expressly granted elsewhere.

In any event, no part of this document may be reproduced in any form without the express written consent of the copyright holders.

UNIVERSITY OF SASKATCHEWAN. PROPRIETARY AND CONDIDENTIAL | Page 3 of 9

## Table of Contents

# Requirement Specification

This section outlines the functional and performance requirements of the system, detailing the design objectives, operational constraints, and expected behaviors necessary to ensure that the implementation meets its intended purpose.

## Functional Requirements:

The functional requirements for the design and implementation of this project are listed below: Functionality (ID: 01):
Type of Constraint | Requirement Description
Performance/Capability | The robot shall be able to follow the user within a 100 cm radius when not in standby.
Performance/Capability | The robot shall be able to follow the user at a speed of 5 km/h (±1km/h) when following a user.
Performance/Capability | The robot shall be able to carry a payload of up to 25 kg securely during operation.
Performance / Timeliness | The system shall be able to detect and avoid obstacles within 150 cm and reroute to continue following the user.

Hardware (ID: 02):
Type of Constraint | Requirement Description
Performance/Capacity | The system shall be able to accommodate objects not exceeding 50 cm × 40 cm × 25 cm in dimension.
Performance/ Operability | The system shall operate on indoor floor surfaces with coefficient of friction ≥ 0.5 and ≤ 0.9
Performance/ Operability | The system shall operate on indoor floor surfaces with maximum surface unevenness ≤ 5 mm
Performance/ Operability | The system shall operate on indoor floor surfaces with maximum incline ≤ 5°
Performance/ Operability | The system shall operate on indoor floor surfaces with no debris larger than 2 cm

UI (ID: 03):
Type of Constraint | Requirement Description
Functionality / Accessibility | The system shall be able to provide a user interface to start and stop operation.

Power (ID: 04):
Type of Constraint | Requirement Description
Performance / Timeliness | The system should be rechargeable.
Sustainability / Power | The system shall be able to recharge using standard 120 V AC power and reach full charge within 6 hours.
Performance / Power | The system shall be able to last for 4 hours on a single charge cycle under 25 kg load

## Non-Functional Requirements:

The non-functional requirements for the design and implementation of this project are listed below:
Environmental (ID: 05):
Type of Constraint | Requirement Description
Environmental / Operability | The system shall be able to function within enclosed spaces and shall not be exposed to outdoor conditions such as rain, direct sunlight, or uneven terrain.
Environmental / Operability | The system shall be able to operate indoors only, within room temperature (15–30 °C).
Environmental / Operability | The system shall be able to function in an under environmental conditions with noise levels of up to 50dB.

Security (ID: 06):
Type of Constraint | Requirement Description
Security / Data integrity | The system shall not store any visual/audio data of the user.
Security / Access Control | The system shall be able to pair and operate only with authorized user devices or identifiers.

# Design Constraints

The constraints below define the limitations and conditions that influence the system’s design:
1. The system shall be designed for indoor operation only under controlled environmental conditions such as stable temperatures and dry surfaces.
2. The system shall be designed to support navigation only on smooth, flat surfaces to ensure traction and stability.
3. The system shall be limited to operating on a single floor level, without the ability to traverse stairs, ramps, or steep inclines.
4. The system shall be capable of carrying a payload of not more than 1kg while maintaining stable motion on smooth surfaces.
5. The system shall be developed within a total budget not exceeding $1000 CAD.
6. The system design shall accommodate a maximum object size of 50cm x 40cm x 25cm.
7. The system shall be battery-powered and rechargeable using a standard electrical outlet.

# APPENDIX I: KEY REQUIREMENTS

Requirement # | R01-01
Requirement Type: | Functional
Description: | The robot shall be able to follow the user within a 100m radius when not in standby.
Originator: | Client (G5)
Fit Criterion: | The robot maintains a following distance within a 100m radius from the user during motion, verified through testing in an indoor environment.
Priority: | 1
Conflicts: | None
History: | Date Created: 8th October, 2025 Adjusted for Final Design: 7th April, 2026
Requirement # | R01-02
Requirement Type: | Functional
Description: | The robot shall be able to carry a payload of up to 25 kg securely during operation.
Originator: | Client (G5)
Fit Criterion: | The robot shall successfully transport a payload of 25 kg without loss of balance, slippage, or system malfunction over a continuous operation period on a smooth indoor surface.
Priority: | 2
Conflicts: | None
History: | Date Created: 8th October, 2025 Adjusted for Final Design: 7th April, 2026

Requirement # | R01-03
Requirement Type: | Functional
Description: | The system shall be able to detect and avoid obstacles within not less than 150cm and reroute to continue following the user.
Originator: | Client (G5)
Fit Criterion: | During testing, the system consistently detects obstacles at a minimum distance of 40 cm and successfully adjusts its path to avoid collision while maintaining continuous user tracking.
Priority: | 3
Conflicts: | None
History: | Date Created: 9th October, 2025 Adjusted for Final Design: 7th April, 2026
Requirement # | R02-01
Requirement Type: | Hardware
Description: | The system shall operate on indoor floor surfaces with coefficient of friction ≥ 0.5 and ≤ 0.9
Originator: | Client (G5)
Fit Criterion: | The system shall demonstrate stable motion, including forward movement, turning, and stopping, on indoor surfaces with a coefficient of friction between 0.5 and 0.9, without wheel slippage or loss of control during operation.
Priority: | 4
Conflicts: | None
History: | Date Created: 9th October, 2025 Adjusted for Final Design: 7th April, 2026

Requirement # | R02-02
Requirement Type: | Hardware
Description: | The system shall operate on indoor floor surfaces with maximum surface unevenness ≤ 5 mm
Originator: | Client (G5)
Fit Criterion: | The system shall successfully traverse indoor surfaces with surface unevenness up to 5 mm over a continuous path of at least 5 m, without loss of stability, tipping, or degradation in tracking performance.
Priority: | 5
Conflicts: | None
History: | Date Created: 7th April, 2026
Requirement # | R02-03
Requirement Type: | Hardware
Description: | The system shall operate on indoor floor surfaces with maximum incline ≤ 5°
Originator: | Client (G5)
Fit Criterion: | The system shall demonstrate continuous operation on an inclined surface of up to 5°, maintaining controlled movement, stable speed, and accurate user-following behavior without rollback or instability.
Priority: | 6
Conflicts: | None
History: | Date Created: 7th April, 2026

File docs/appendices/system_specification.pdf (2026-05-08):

DEPARTMENT OF ELECTRICAL AND COMPUTER ENGINEERING UNIVERSITY OF SASKATCHEWAN
ECE495-2025G503 | VERSION 0.1 | SYSTEM SPECIFICATION

© Chidubem Emeka-Nwuba, Aneek Mohamed Ruksan, Aditya Ramakrishnan, Ethan D’Almeida.

This document is CONFIDENTIAL and PROPRIETARY and is for the use of University of Saskatchewan personnel only, except to the extent that permission is expressly granted elsewhere.

In any event, no part of this document may be reproduced in any form without the express written consent of University of Saskatchewan.

UNIVERSITY OF SASKATCHEWAN. PROPRIETARY AND CONDIDENTIAL | Page 1 of 13
DOC NO: | ECE495-20250503 | ISSUE DATE: | 23-10-2025
FILE NAME: | g5_assign3_system_specification.pdf | VERSION NO: | 0.1
FILING PATH: | https://github.com/AneekMubarak/MobileToolAssistant/blob/main/docs/
TITLE: | SYSTEM SPECIFICATION
PROJECT: | MOBILE TOOL ASSISTANT
KEYWORDS: | Test Plan, Decision Matrix, Justification, Block Diagram, Robots, System Specifications

APPROVED BY

Daniel Teng | Date
Customer

PREPARED BY:

Chidubem Emeka-Nwuba | Date
Design Engineer
Aditya Ramakrishnan | Date
Design Engineer
Aneeq Mohamed Ruksan | Date
Design Engineer
Ethan D’Almeida | Date
Design Engineer

REVIEWED BY:

Chandler Janzen | Date
Supervisor

© Chidubem Emeka-Nwuba, Aneek Mohamed Ruksan, Aditya Ramakrishnan, Ethan D’Almeida.

This document is CONFIDENTIAL and PROPRIETARY and is for the use of University of Saskatchewan personnel only, except to the extent that permission is expressly granted elsewhere.

In any event, no part of this document may be reproduced in any form without the express written consent of University of Saskatchewan.

UNIVERSITY OF SASKATCHEWAN. PROPRIETARY AND CONDIDENTIAL | Page 2 of 13

REVISION HISTORY
Version No. | Date | Originator | Summary of Changes
1 | 23-10-2025 | C.E.N, A.R, E.D, A.M.R | Document created
2 | 30-03-2025 | E.D | Updated all block diagrams for alternatives

© Chidubem Emeka-Nwuba, Aneek Mohamed Ruksan, Aditya Ramakrishnan, Ethan D’Almeida.

This document is CONFIDENTIAL and PROPRIETARY and is for the use of University of Saskatchewan personnel only, except to the extent that permission is expressly granted elsewhere.

In any event, no part of this document may be reproduced in any form without the express written consent of University of Saskatchewan.

UNIVERSITY OF SASKATCHEWAN. PROPRIETARY AND CONDIDENTIAL | Page 3 of 13

\

## Table of Contents

Overview of the System | 4
Functional Block Diagram | 5
Functional Description | 6
System Test Plan | 7
APPENDIX I: SYSTEM ALTERNATIVE | 9
APPENDIX A: Aditya Ramakrishnan (Alternative-1) | 9
APPENDIX B: Ethan D’Almeida (Alternative-2) | 10
APPENDIX C: Chidubem Emeka-Nwuba (Alternative-3) | 11
APPENDIX D: Aneek Mohamed Ruksan (Alternative-4) | 12
APPENDIX 2: ANALYSIS OF SYSTEM ALTERNATIVES | 13

## List of Figures

Figure 1: Functional Block Diagram | 5
Figure 2: Alternative 1 - Block Diagram | 9
Figure 3: Alternative 2 - Block Diagram | 10
Figure 4: Alternative 3 - Block Diagram | 11
Figure 5: Alternative 4 - Block Diagram | 12

## List of Tables

Table 1: Functional Tests | 7
Table 2: Hardware Tests | 7
Table 3: User Interface Test | 7
Table 4: Power and Charging Tests | 8
Table 5: Non-Functional tests | 8
Table 6: Decision Matrix | 13

## Overview of the System

The Mobile Tool Assistant is an autonomous robot designed to follow a user within a short range while carrying small tools or materials. It uses Ultra-Wide Band (UWB) based localization to maintain a consistent distance from an authorized user and integrates onboard sensing and control logic to navigate safely in an indoor environment.

The system consists of a mobile base with drive motors, embedded processing hardware, and sensors for environmental awareness. Its primary function is to automatically follow a user while carrying a payload and taking actions to avoid obstacles. The robot operates entirely autonomously once it starts and would alert the user when the battery level drops below 10%.

The system architecture emphasizes modularity: a tracking subsystem estimates the user’s relative position, a control subsystem computes motion commands, and a power subsystem manages energy distribution and charging. All components communicate through a central processing unit that ensures real-time response and safety compliance.

The proposed solution satisfies the project requirements by:
- Maintaining autonomous, reliable short-range following feature using UWB distance estimation.
- Providing safety through automatic obstacle avoidance and controlled motion.
- Supporting energy-efficient operation and charging features.
This high-level design provides a balance between practicality, cost, and technical feasibility while ensuring the robot can operate within the constraints outlined in the requirements specification.

## Functional Block Diagram

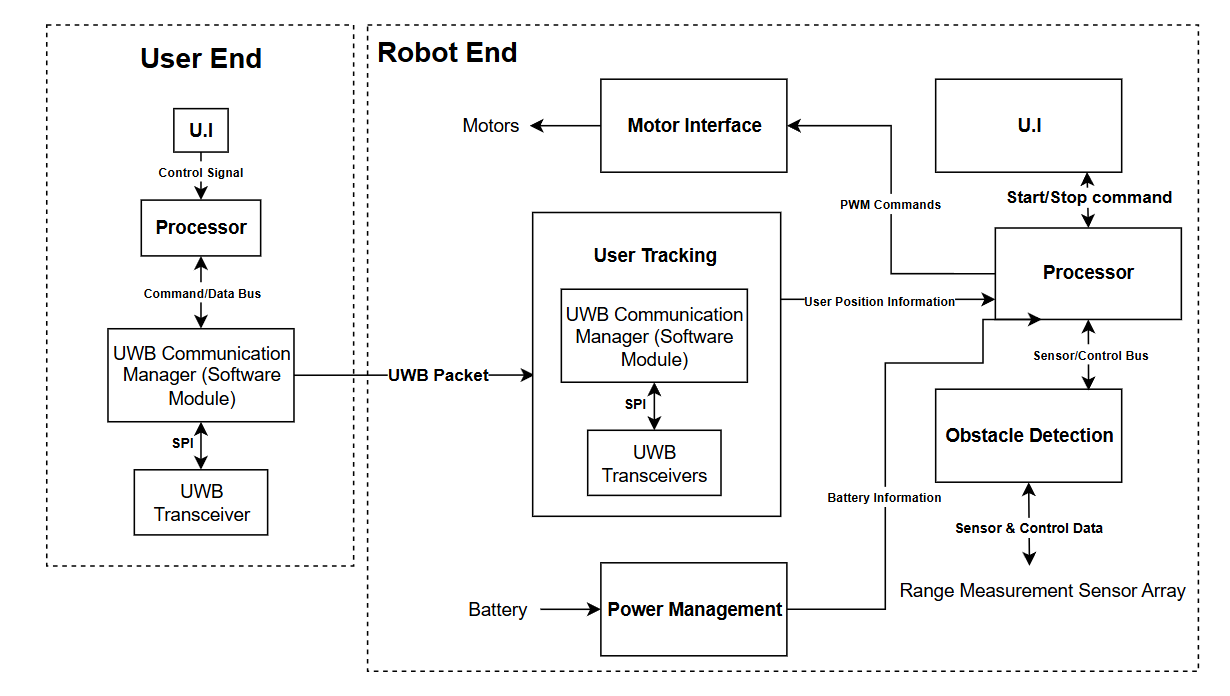
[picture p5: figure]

Figure 1: Functional Block Diagram

## Functional Description

The system is divided into six main subsystems that collectively achieve user following, motion control, and operational safety.

1. User Tracking Subsystem
Determines the user’s relative position using UWB distance data.
Inputs: UWB range signals.
Outputs: Estimated relative user position and movement direction.
Requirement: Maintain continuous communication within ~10 m range with minimal delay.
2. Navigation Subsystem
Collects environmental data to detect obstacles.
Inputs: Range sensor data.
Outputs: Distance/Proximity flags.
Requirement: Provide timely updates for collision-free motion.
3. Motion Control Subsystem
Convert data into drive commands.
Inputs: Desired following distance, obstacle data.
Outputs: Motor and steering signals.
Requirement: Achieve stable, smooth, and responsive movement.
4. Processing and Communication Subsystem
Acts as the core controller for coordinating all subsystems.
Inputs: Data from tracking, sensors, and user controls.
Outputs: Status updates, and telemetry.
Requirement: Perform real-time decision-making with efficient data handling.
5. Power Management Subsystem
Regulates and distributes electrical power to system components.
Inputs: Battery supply.
Outputs: Stable voltage lines to other subsystems and battery information. Requirement: Ensure safe operation and adequate runtime.
6. User Interface Subsystem
Provides manual control and feedback to the user.
Inputs: Buttons or wireless control signals.
Outputs: Indicators for mode, status, and battery level. Requirement: Offer simple, reliable interaction during operation.

## System Test Plan

Table 1: Functional Tests
Test ID | Requirement | Test Objective | Test Method / Procedure | Expected Result
F1 | Follow distance: 1 m ± 0.5 m | Verify the robot maintains proper following distance from the user node. | Place the user node at varying distances (0.5–2 m). Measure and record actual following distance over time. | Robot maintains an average distance of 1 m ± 0.5 m in all trials.
F2 | Follow speed: 5 km/h ± 1 km/h | Verify the robot’s ability to follow a moving user within specified speed. | Move the user at incremental speeds up to 6 km/h. Measure robot’s response lag and following accuracy. | Robot maintains tracking and motion synchronization within the specified speed tolerance.
F3 | Payload: 5 kg capacity | Validate payload-carrying capability during motion. | Place payloads of up to 5 kg on the platform and repeat follow tests. | Robot moves smoothly without mechanical strain or loss of control.
F4 | Obstacle detection | Verify obstacle detection and avoidance. | Place static obstacles within 1.0 m in robot path. Record detection and response. | Robot detects obstacle ≥1.0 m away and responds accordingly.

Table 2: Hardware Tests
Test ID | Requirement | Test Objective | Test Method / Procedure | Expected Result
H1 | Payload Size limit: 30×20×15 cm | Confirm ability to carry payload of given dimensions | Measure payload dimensions. | Robot moves smoothly without mechanical strain or loss of control.
H2 | Surface navigation | Validate navigation on flat indoor surfaces. | Operate robot on a smooth surface. | Robot navigates without slipping, stalling, or losing balance.

Table 3: User Interface Test
Test ID | Requirement | Test Objective | Test Method / Procedure | Expected Result
UI1 | Start/stop interface | Validate user control of operation. | Activate robot via user interface. Observe response. | Robot starts and stops following reliably upon user input.

Table 4: Power and Charging Tests
Test ID | Requirement | Test Objective | Test Method / Procedure | Expected Result
P1 | Charging input and time | Verify charging operation with 120 V AC supply. | Connect charger to standard outlet, measure total recharge time. | Full charge achieved within 6 hours.
P2 | Battery runtime | Validate operating duration. | Fully charge battery, operate continuously in follow mode. | Robot operates for ≥2 hours on a single charge.

Table 5: Non-Functional tests
Test ID | Requirement | Test Objective | Test Method / Procedure | Expected Result
NF1 | Indoor-only operation | Verify safe and reliable operation indoors. | Test operation in different rooms and lighting conditions. | Robot functions stably indoors; avoids failure under typical lighting.
NF2 | Temperature tolerance | Validate operation in standard indoor range. | Run robot in environments between 20–25°C. | Normal operation within temperature range; no performance degradation.
NF3 | Noise compliance | Measure sound level during operation. | Use sound meter during motion. | Noise level ≤ 50 dB.
NF4 | Data privacy | Verify no user data stored. | Inspect firmware and logs for any visual/audio capture. | No personal data stored or transmitted.
NF5 | Authorized pairing | Verify restricted pairing behavior. | Attempt to connect unauthorized devices. | Robot accepts only pre-authorized user node connections.

## APPENDIX I: SYSTEM ALTERNATIVE

### APPENDIX A: Aditya Ramakrishnan (Alternative-1)

Overview

A Mobile Tool Assistant that autonomously follows the user using a vision-based tracking system, detects and avoids obstacles with LiDAR. The onboard camera continuously tracks the designated user using a visual marker, while the LiDAR module provides real-time mapping for safe navigation.

Key Features
- Vision-Based Following: Tracks the user through real-time image processing and maintains a consistent following distance using camera-derived position data.
- LiDAR Navigation: Real-time LiDAR scanning allows precise obstacle detection and local path planning.
- Processing: The processing unit fuses vision and LiDAR data to plan paths and control the drive system.
- User Interface: Simple start/stop and mode control via smartphone.
- Safety and Reliability: Obstacle detection and navigation, low-battery alerts.

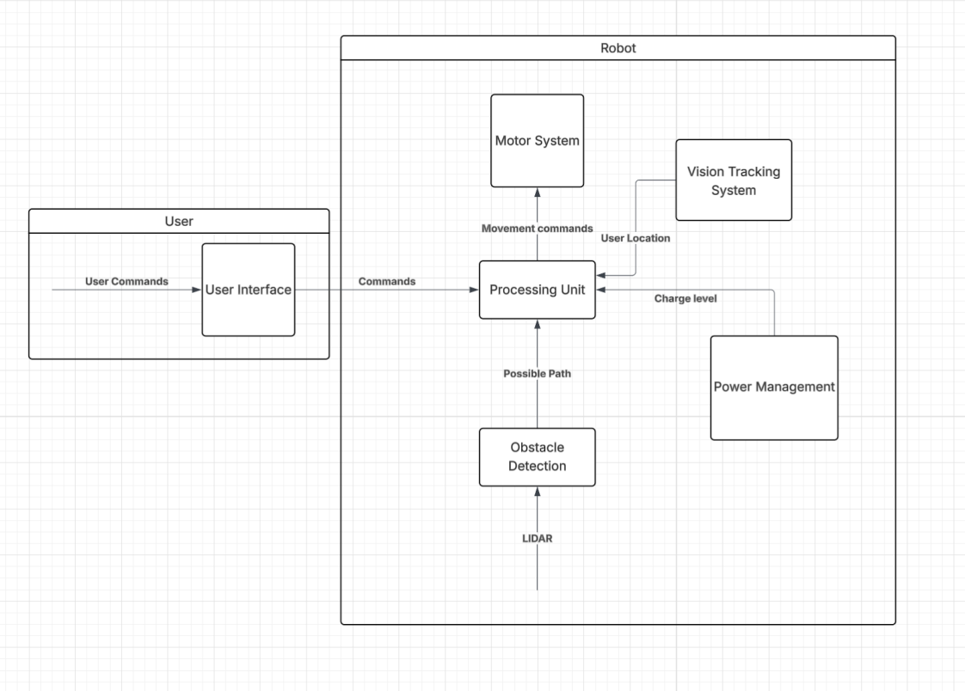
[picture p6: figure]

Figure 2: Alternative 1 - Block Diagram

### APPENDIX B: Ethan D’Almeida (Alternative-2)

Overview
The system is an autonomous robot designed to follow a user carrying a small BLE transmitter while navigating safely in its environment. It combines BLE tracking, sensor-based obstacle detection, and autonomous movement.
Key Features
- BLE based tracking using Direction Finding (Bluetooth 5.1 and above) and RSSI.
- Obstacle detection sensors for close-range obstacle detection along with stereo cameras for long-range obstacles with depth sensing.

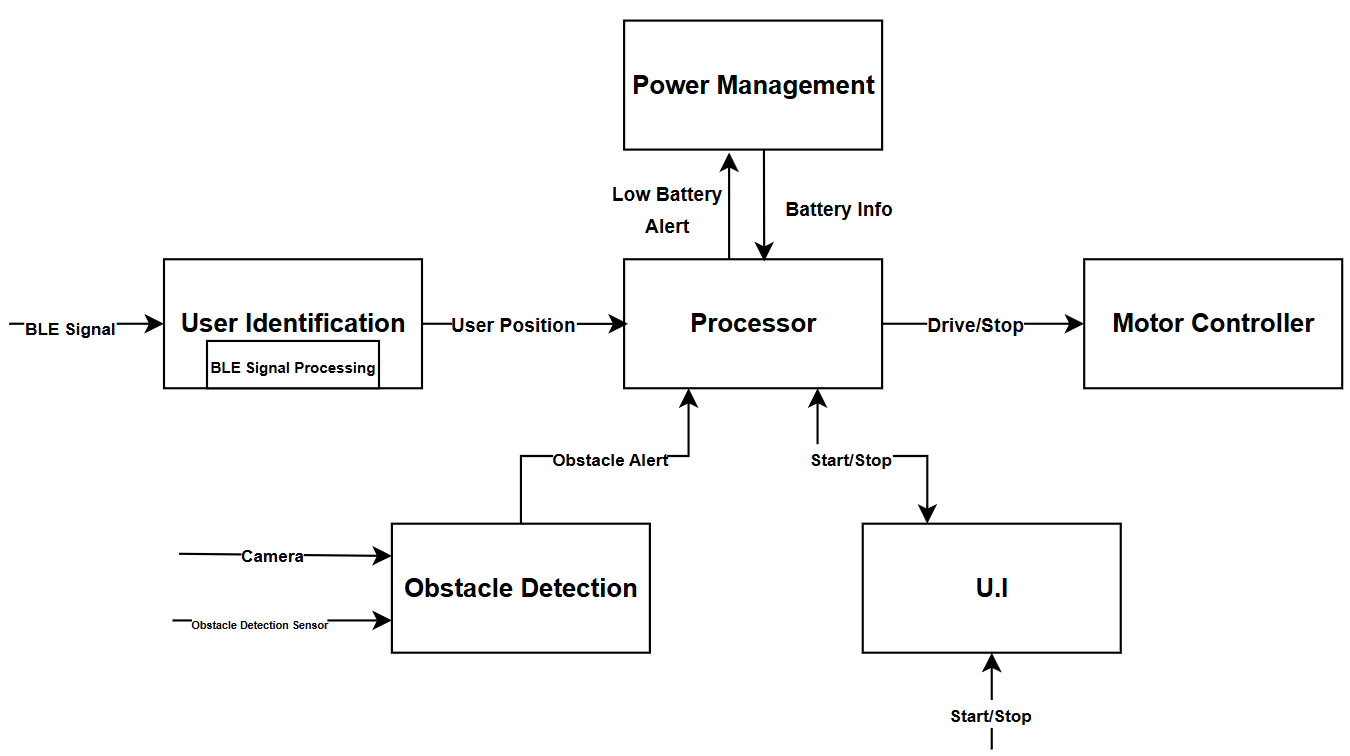
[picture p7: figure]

Figure 3: Alternative 2 - Block Diagram

### APPENDIX C: Chidubem Emeka-Nwuba (Alternative-3)

Overview

The system is an autonomous mobile assistant designed to follow a user wearing a BLE-based wearable device while navigating safely through its environment. It combines BLE communication with IMU-based motion data to track the user’s movement and orientation, while onboard sensors handle real-time obstacle detection and avoidance. The robot platform interprets incoming data to adjust its path and maintain smooth, safe following behavior.

Key Features

- BLE-Based User Tracking: The wearable user node continuously broadcasts motion and orientation data, allowing the robot to interpret user direction and movement in real time.
- Obstacle Detection: Integrated sensing enables the robot to detect obstacles in its path and recover from displacement while maintaining stable navigation.
- Autonomous Motion Control: A central processing unit interprets user and sensor data to control the robot’s motors and execute movement decisions.
- Safety Features: The system identifies potentially unsafe conditions, such as ramps or stairs, to prevent accidental falls or collisions.
- Power Management System: Manages and distributes power across system components and communicates with the processor to report battery status and initiate power-saving actions.
- User Interface System: Software interface that allows the user to start, stop, and monitor operation, utilizing information received from the user node for control.

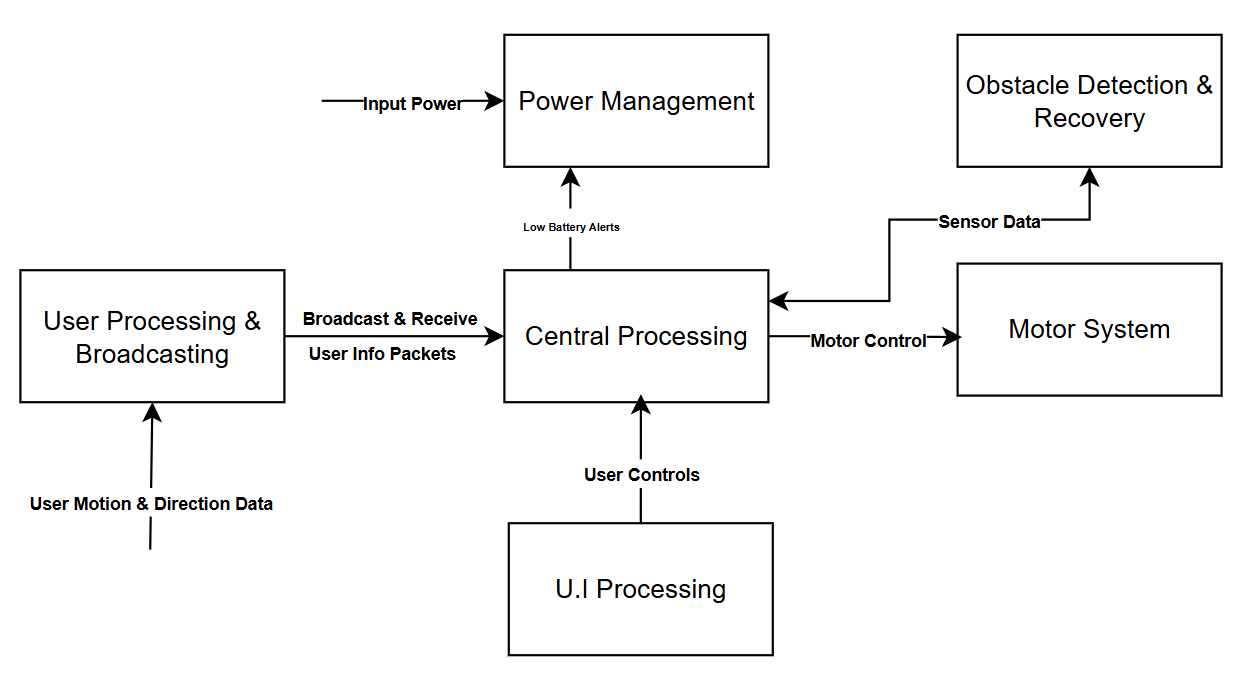
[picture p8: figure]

Figure 4: Alternative 3 - Block Diagram

### APPENDIX D: Aneek Mohamed Ruksan (Alternative-4)

System Overview
The system is an autonomous mobile assistant designed to follow a user carrying a UWB transceiver while navigating safely through its environment. It combines UWB-based tracking, sensor-driven obstacle detection, and autonomous motion control for reliable operation.
Key Features
- UWB-based User Tracking: Reliable short-range communication for user identification and distance estimation.
- Obstacle Detection: Range sensor array for real-time environment scanning and collision avoidance.
- Autonomous Motion Control: Processor-driven motor interface for path following and maneuvering.
- Dual User Interfaces: Remote (wearable) and onboard UI for control options.

Figure 5: Alternative 4 - Block Diagram

## APPENDIX 2: ANALYSIS OF SYSTEM ALTERNATIVES

Table 6: Decision Matrix
Criteria | Weight | Alt-1 | Alt-2 | Alt-3 | Alt-4
Hardware Cost | 4 | 6 | 7 | 9 | 8
Development Time | 5 | 4 | 4 | 5 | 4
Power Consumption | 4 | 3 | 7 | 8 | 8
Ease of Use | 3 | 6 | 6 | 7 | 8
Reliability | 5 | 4 | 8 | 5 | 4
Scalability | 4 | 8 | 6 | 4 | 5
Final Score | 126 | 158 | 155 | 137

Each proposed system alternative was analyzed based on its ability to meet the project’s technical, economic, and operational requirements. The key evaluation criteria included hardware cost, development time, power consumption, ease of use, reliability, and scalability. Each criterion was weighed on a scale of 1 to 5 according to its importance, and the alternatives were scored out of 10 based on performance under each category. The resulting weighted scores provided an objective comparison of overall feasibility.

From the analysis, Alternative 4 (UWB-based system) achieved the highest overall score (158), demonstrating the best balance between technical performance and practicality. UWB communication offers superior distance accuracy and reliability compared to BLE and vision-based tracking, while maintaining moderate cost and power usage.

Alternative 3 (BLE + IMU system) followed closely with 155 points, offering excellent power efficiency and affordability but with limited positional precision due to RSSI fluctuations. Alternative 1 (Vision + LiDAR system) and Alternative 2 (BLE + stereo vision system) provided strong technical capability but were less economical and more power-intensive, making them less suitable for a compact, low-cost prototype.

In summary, Alternative 4 was selected as the final design due to its high reliability, strong technical accuracy, and overall balance across all weighted criteria. It best meets the project’s objectives while remaining feasible for further development and integration.

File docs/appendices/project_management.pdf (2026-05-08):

DEPARTMENT OF ELECTRICAL AND COMPUTER ENGINEERING UNIVERSITY OF SASKATCHEWAN
ECE495-2025G5 | VERSION 0.1 | MOBILE TOOL ASSISTANT

© 2025 Chidubem Emeka-Nwuba, Aneek Mohamed Ruksan, Aditya Ramakrishnan, Ethan D’Almeida.

This document is CONFIDENTIAL and PROPRIETARY and is for the use of University of Saskatchewan personnel only, except to the extent that permission is expressly granted elsewhere.

In any event, no part of this document may be reproduced in any form without the express written consent of University of Saskatchewan.

UNIVERSITY OF SASKATCHEWAN. PROPRIETARY AND CONDIDENTIAL | Page 1 of 9
DOC NO: | ECE495-2025G5 | ISSUE DATE: | 07-04-2026
FILE NAME: | g5_project_management | VERSION NO: | 0.1
FILING PATH: | https://github.com/AneekMubarak/MobileToolAssistant/tree/main/docs
TITLE: | Project Management
PROJECT: | MobileToolAssistant
KEYWORDS: | Management, PMI, Risk

APPROVED BY

Daniel Teng | Date
Customer

PREPARED BY:

Aditya Ramakrishnan | Date
Design Engineer
Aneek Mohamed Ruksan | Date
Design Engineer
Chidubem Emeka-Nwuba | Date
Design Engineer
Ethan D’Almeida | Date
Design Engineer

REVIEWED BY:

Chandler Janzen | Date
Supervisor

© 2025 Chidubem Emeka-Nwuba, Aneek Mohamed Ruksan, Aditya Ramakrishnan, Ethan D’Almeida.

This document is CONFIDENTIAL and PROPRIETARY and is for the use of University of Saskatchewan personnel only, except to the extent that permission is expressly granted elsewhere.

In any event, no part of this document may be reproduced in any form without the express written consent of University of Saskatchewan.

UNIVERSITY OF SASKATCHEWAN. PROPRIETARY AND CONDIDENTIAL | Page 2 of 9

REVISION HISTORY
Version No. | Date | Originator | Summary of Changes
1 | 07-04-2026 | E.D | Document created

## Table of Contents

Project Overview | 4
Team Governance and Roles | 4
Project Monitoring and Supervisor Meetings | 5
Financial and Resource Tracking | 5
Development Resources | 6
Scheduling, Monitoring, and Control | 6
Risk Issue and Management | 8
Project Closure and Lessons Learned | 9

## List of Tables

Table 1: Individual Member Contribution Summary | 4
Table 2: Bill of Materials | 5
Table 3: Description of Planned v/s Actual Hours and Deadlines | 7
Table 4: Identified Risks and corresponding Mitigation Strategies | 8

## List of Figures

Figure 1: Gantt Chart of Expected v/s Actual Project Schedule | 6

## Project Overview

The objective of the Mobile Tool Assistant project was to deliver a proof-of-concept mobile robotic prototype capable of autonomously following a designated worker and transporting a tool payload of up to 25 kg in an indoor industrial environment.
During initial supervisor meetings (October 2025), the team made strategic decisions to eliminate features such as an auto-docking/return-to-base function to ensure the project remained feasible within the timeframe.
- Budget Constraint: $1000 CAD maximum.
- Schedule Constraint: Completion within the academic year (November 2025 – March 2026).
- Scope Boundaries: Operations restricted to flat, single-level indoor environments at safe walking speeds (≤ 5 km/h). Vision-based and BLE-based tracking alternatives were scoped out in favor of UWB (Ultra-Wideband) tracking to balance cost and accuracy.

## Team Governance and Roles

A four-member engineering team executed the project. Project governance relied on a structure in which tasks were divided by subsystem requirements, and integration was handled collaboratively.

Table 1: Individual Member Contribution Summary

Member | Total Hours | Key Contributions
Aneek Mohamed Ruksan | 180 | UWB User Tracking, UI/User Node
Aditya Ramakrishnan | 120 | Motor Control Algorithm, Power Management System, Obstacle Avoidance, Chassis Design and Printing, System Refining and Improvement, System Assembly
Ethan D’Almeida | 70 | UWB calibration support and testing, documentation, obstacle detection, and avoidance improvements
Chidubem Emeka-Nwuba | 75 | Obstacle Detection Subsystem Assembly and Integration, Software architecture: implementation, management, and subsystem task integration

## Project Monitoring and Supervisor Meetings

To ensure the project stayed on track, the team held regular design and status meetings with the Project Supervisor, Chandler Janzen. These meetings served as the primary way we tracked project progress and issue tracking.
Summary of Key Meeting Outcomes:
- Oct 03, 2025 (Requirements Phase): Focused on defining testable, quantifiable requirements. Identified the risk of scope creep and decided to strictly limit the operational environment to indoors with a 5 km/h speed limit.
- Oct 21, 2025 (System Alternatives Phase): Addressed potential safety hazards (stairs/holes). Decided to minimize mechanical design details and remove the auto-docking requirement to reduce overall scope and focus on electronic/control feasibility.
- Nov 04, 2025 (Project Planning Phase): Clarified testing metrics (e.g., using a decibel meter for noise constraints).
- Nov 25, 2025 (Detailed Design Phase): Established documentation standards, requiring every requirement to map directly to a design element with clearly defined subsystem inputs/outputs.
- Feb 26, 2026 (Execution & Testing Phase): Conducted a prototype demonstration. Logged critical issues regarding UWB module calibration inconsistencies, motor alignment, and chassis mounting.

### Financial and Resource Tracking

The project was controlled to remain under the $1000 CAD constraint. Financial planning involved estimating material costs early in the design phase and adjusting based on part availability. Table 2: Bill of Materials

Part Name | Quantity | Cost (in CAD)
STM32 Dev Board | 1 | $42.65
DWM1000 Module (UWB) | 3 | $122.91
VL531X Module (ToF) | 3 | $64.77
L298N Motor Driver | 1 | $11.78
ESP8266 | 1 | $4.05
TT DC Gear Motor | 2 | $4.00
Buck Converter Module | 1 | $21.99
Rechargeable Li-ion Battery | 2 | $21.40
Small Yellow Button | 1 | $0.27
Total | | $293.82

## Development Resources

- Hardware: Multimeter, Soldering Iron, BambuLab P1-S (for chassis).
- Software: STM32Cube IDE v1.19.0, Arduino IDE v2.3.7, Serial Debug Assistant, GitHub (version control).

## Scheduling, Monitoring, and Control

The project timeline experienced significant deviations from the initial baseline plan. By actively monitoring the schedule, the team was able to apply mitigation strategies such as simplifying the UI and running tasks in parallel to ensure final delivery.

Figure 1: Gantt Chart of Expected v/s Actual Project Schedule

Planned
Actual

Expected vs Actual Project Schedule

Legend

Task | November | December | January | February | March

Detailed Design

Part Selection and Ordering

UWB Tracking Module/User Tracking

Obstacle Detection

Motion Control Algorithm

User Interface (and User Node Assembly)
Power Management System

System Assembly and Integration (Constructing Prototype) Chassis Design and Printing

System Testing and Debugging

System Refining and Performance Improvement

Table 3: Description of Planned v/s Actual Hours and Deadlines

Task ID | Task Name | Planned Hours | Planned Deadline | Actual Hours | Actual Completion | Comments
1 | Detailed Design | 20h | 27th Nov, 2025 | 20h | 27th Nov, 2025 | On time
2 | Part Selection and Ordering | 10h | 1 st Dec, 2025 | 25h | 27th Jan, 2026 | Delayed due to redesigns and part availability
3 | UWB Tracking Module | 40h | 21st Jan, 2026 | 175h | 12th Mar, 2026 | Required extra time for antenna delay calibration, DS-TWR algorithm.
4 | Obstacle Detection | 45h | 21st Jan, 2026 | 45h | 4 th Mar, 2026 | Integrating multiple ToF sensors
5 | Motion Control Algorithm | 21h | 30th Jan, 2026 | 43h | 24th Mar, 2026 | Delayed due to motor alignment and integration with UWB
6 | User Interface | 20h | 30th Jan, 2026 | 5h | 13th Mar, 2026 | Saved time here, but overall, UWB cascading delay
7 | Power Management System | 24h | 21st Jan, 2026 | 24h | 20th Mar, 2026 | UWB cascading delay
8 | System Assembly and Integration | 30h | 15th Feb, 2026 | 30h | 23rd Mar, 2026 | UWB cascading delay
9 | Chassis Design and Printing | 15h | 15th Feb, 2026 | 15h | 19th Mar, 2026 | UWB cascading delay
10 | System testing and debugging | 37h | 28th Feb, 2026 | 40h | 24th Mar, 2026 | Delay to ensure stability
11 | System Refining and Improvement | 16h | 28th Feb, 2026 | 37h | 24th Mar, 2026 | More time to refine the motor movements and obstacle detection algorithm

## Risk Issue and Management

Table 4: Identified Risks and corresponding Mitigation Strategies

Identified Risk | Impact | Occurrence/Mitigation Strategy
UWB (new technology) | High | UWB implementation took more hours than planned since it was the new technology we were working with, which caused a chain of long delays. Mitigation: Ethan supported Aneek with calibration while other team members worked on power and obstacle detection in parallel to continue project progress.
Component Availability and Delivery | Medium | Parts Selection took longer than expected due to availability. Mitigation: Critical components were identified and ordered early.
System Integration Issues | High | Integration of motion control and user tracking subsystems took longer than expected due to motor alignment and algorithm issues. Mitigation: Extensive testing was done for each subsystem to fix any issues before fully integrating both systems.
Schedule Overruns | High | Occurred

## Project Closure and Lessons Learned

The project successfully delivered a working proof-of-concept that met the core functional requirements, passing final testing for follow distance (1m ± 0.5m radius), speed (up to 5 km/h), payload capacity (25kg), and obstacle detection (within 150cm).

Throughout the development of the Mobile Tool Assistant, the team identified several key lessons and areas for architectural improvement. Most notably, the team drastically underestimated the learning curve and complexity of implementing custom Ultra-Wideband (UWB) tracking from scratch, highlighting the need in future projects to allocate significantly more schedule buffer for researching and calibrating unfamiliar communication protocols. On the hardware front, relying on jumper wires and protoboards helped with rapid prototyping but introduced signal instability and loose connections during physical testing; future iterations must transition to custom PCBs to ensure electrical reliability and mechanical robustness. Additionally, the prototype's sensor, utilizing front-facing Time-of-Flight (ToF) sensors and two UWB anchors, limited the robot to a 180° field of view, leaving it vulnerable if the user moved behind it. A production model would require a 360° LIDAR sensor and a third rear UWB anchor to achieve full coverage. Finally, upgrading the power system from standard rechargeable AA batteries to an integrated, industry-standard lithium-ion battery pack with a dedicated Battery Management System will be essential to improve energy density and long-term operational performance.

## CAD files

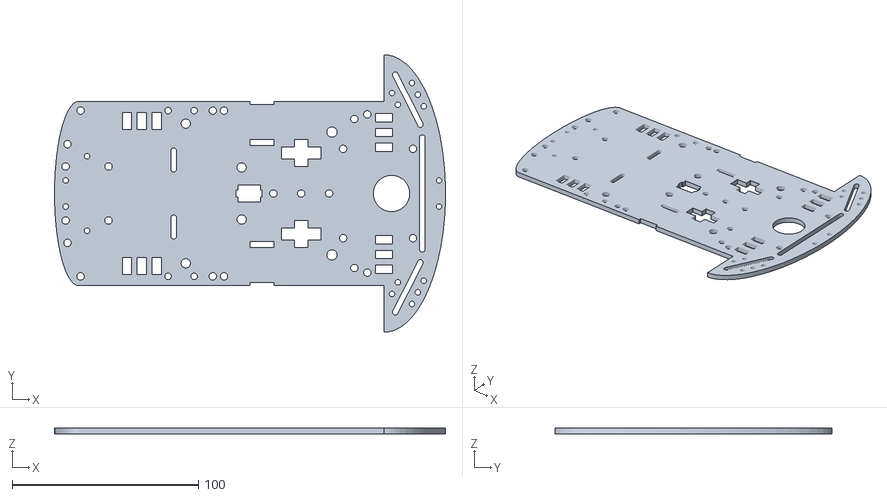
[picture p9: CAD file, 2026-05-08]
docs/design/3d_schematics/Chassis.stl
210.0 x 149.0 x 3.00

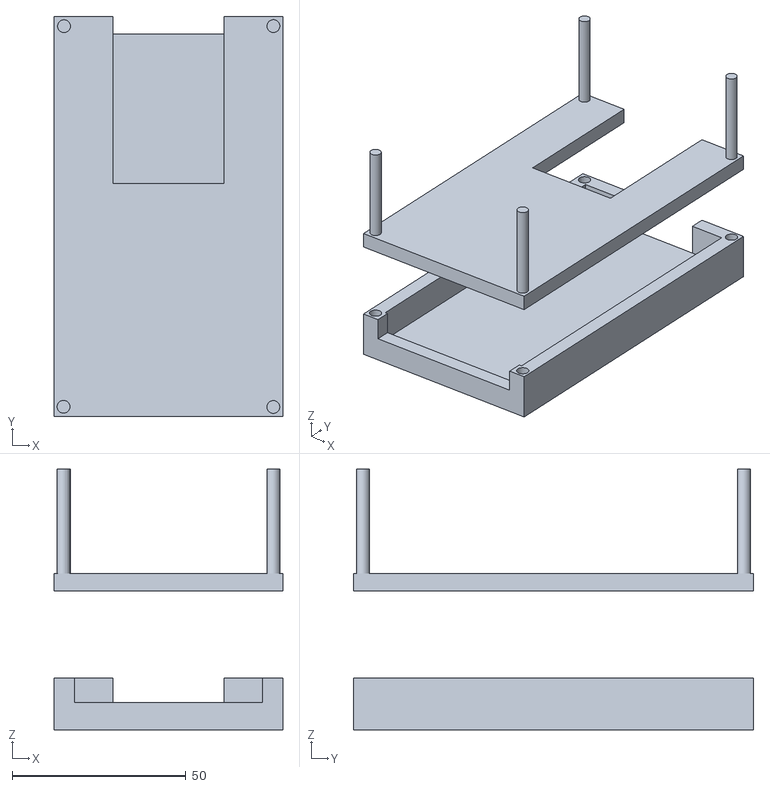
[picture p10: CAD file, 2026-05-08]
docs/design/3d_schematics/Case.stl
65.8 x 115.0 x 75.0

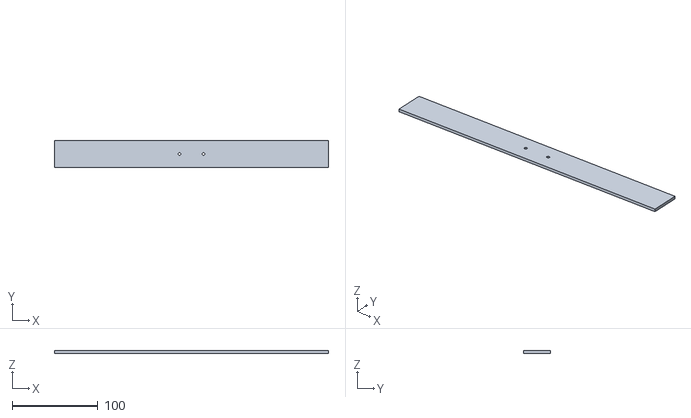
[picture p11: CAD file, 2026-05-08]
docs/design/3d_schematics/RobotArmStart v1.stl
320.0 x 32.0 x 3.00

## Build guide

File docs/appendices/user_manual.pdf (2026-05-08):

© Chidubem Emeka-Nwuba, Aneek Mohamed Ruksan, Aditya Ramakrishnan, Ethan D’Almeida.

This document is CONFIDENTIAL and PROPRIETARY and is for the use of the copyright holders, except to the extent that permission is expressly granted elsewhere.

In any event, no part of this document may be reproduced in any form without the express written consent of the copyright holders.

UNIVERSITY OF SASKATCHEWAN. PROPRIETARY AND CONFIDENTIAL | Page 1 of 23

# Mobile Tool Assistant User Manual

© Chidubem Emeka-Nwuba, Aneek Mohamed Ruksan, Aditya Ramakrishnan, Ethan D’Almeida.

This document is CONFIDENTIAL and PROPRIETARY and is for the use of the copyright holders, except to the extent that permission is expressly granted elsewhere.

UNIVERSITY OF SASKATCHEWAN. PROPRIETARY AND CONFIDENTIAL | Page 2 of 23

## Contents

© Chidubem Emeka-Nwuba, Aneek Mohamed Ruksan, Aditya Ramakrishnan, Ethan D’Almeida.

This document is CONFIDENTIAL and PROPRIETARY and is for the use of the copyright holders, except to the extent that permission is expressly granted elsewhere.

UNIVERSITY OF SASKATCHEWAN. PROPRIETARY AND CONFIDENTIAL | Page 3 of 23

## List of Figures

Figure 3: Cycling through power modes using the SET button to select USB output mode. 12 Figure 4: USB output enabled indicated by active current draw and USB indicator LED..... 13

Figure 6: Robot powered on with active voltage output and current draw displayed ........ 15

© Chidubem Emeka-Nwuba, Aneek Mohamed Ruksan, Aditya Ramakrishnan, Ethan D’Almeida.

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

UNIVERSITY OF SASKATCHEWAN. PROPRIETARY AND CONFIDENTIAL | Page 4 of 23

## Introduction

Thank you for using the Mobile Tool Assistant. This robot is designed to carry tools and follow you through indoor workspaces, so you can move tools or materials more efficiently while keeping your hands free for setup, inspection, and task work.
This manual explains how to prepare, operate, charge, inspect, and maintain your robot. For best results, review the Quick Start Guide first, then use the later sections for detailed operating and maintenance instructions.

© Chidubem Emeka-Nwuba, Aneek Mohamed Ruksan, Aditya Ramakrishnan, Ethan D’Almeida.

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

UNIVERSITY OF SASKATCHEWAN. PROPRIETARY AND CONFIDENTIAL | Page 5 of 23

## Environmental Constraints

Your robot performs best when you use it in a clean, predictable indoor environment with enough open floor space for smooth following and turning.

- Use your robot on level indoor flooring such as sealed concrete, tile, vinyl, laminate, or short industrial carpet.
- Keep your path reasonably clear so the robot can move beside or behind you without unnecessary stops.
- Use the robot in dry conditions and keep it away from standing water, spills, and wet cleaning zones.
- Give the robot enough turning space around benches, carts, shelves, and corners.
- Keep loose cables, rags, packaging, and small floor obstacles out of the robot’s travel path.
- Operate in normal indoor lighting so you can monitor movement and respond quickly if you need to stop the robot.

© Chidubem Emeka-Nwuba, Aneek Mohamed Ruksan, Aditya Ramakrishnan, Ethan D’Almeida.

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

UNIVERSITY OF SASKATCHEWAN. PROPRIETARY AND CONFIDENTIAL | Page 6 of 23

## System Overview

Your Mobile Tool Assistant system includes the main robot platform and the parts you need for normal operation.

Component | Description
Main robot chassis | The mobile base that carries your tool load and contains the drive system, control electronics, and frame.
Tool Platform (Payload) | The area where you place the tools or payload the robot is intended to transport.
User-tracking sensors (Robot End) | The sensing hardware used to detect and follow your position. This includes 2 UWB sensors.
User Remote | The remote that allows the robot to follow your movement. This includes a UWB sensor and a STANDBY toggle button
Obstacle detection sensors | The forward sensors used to detect nearby obstacles and trigger avoidance or stopping. This includes 3 distance sensors
Power management module | The buck converter mounted on the robot. It serves as the main power control point and provides a visual indication of battery status.
Rechargeable AA Batteries (Robot End) | The power source for the drive system and onboard electronics.

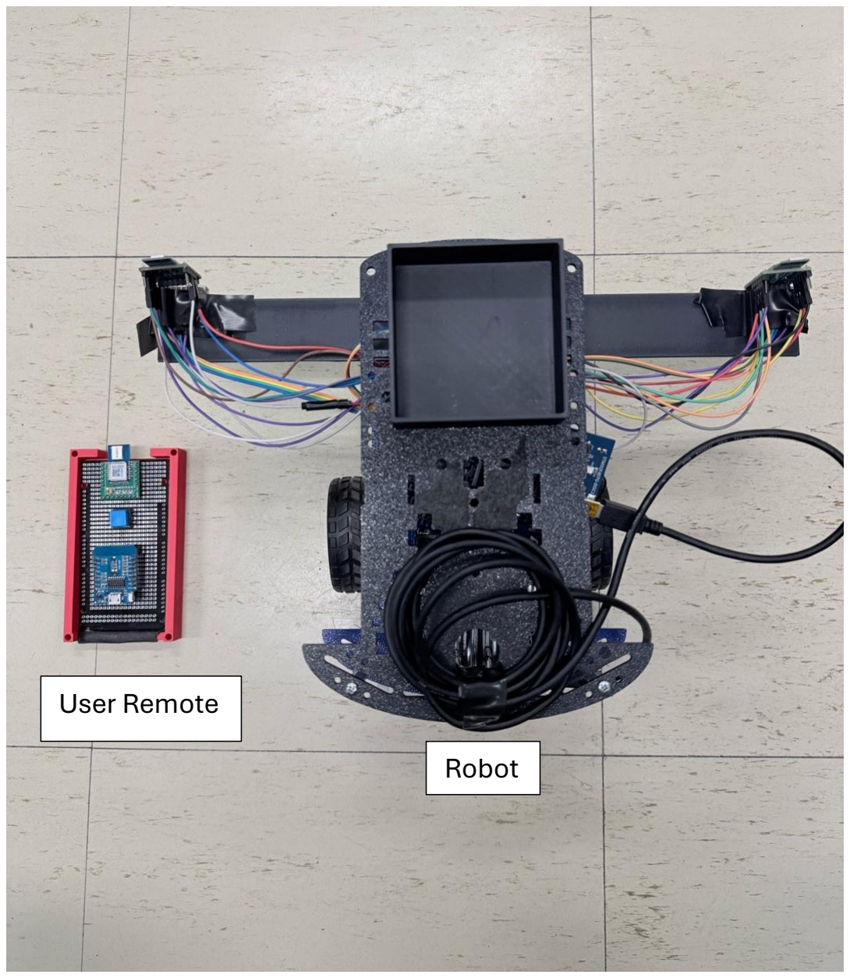
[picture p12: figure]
User Remote; Robot

© Chidubem Emeka-Nwuba, Aneek Mohamed Ruksan, Aditya Ramakrishnan, Ethan D’Almeida.

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

UNIVERSITY OF SASKATCHEWAN. PROPRIETARY AND CONFIDENTIAL | Page 7 of 23

Figure 1: Top view of user remote and robot

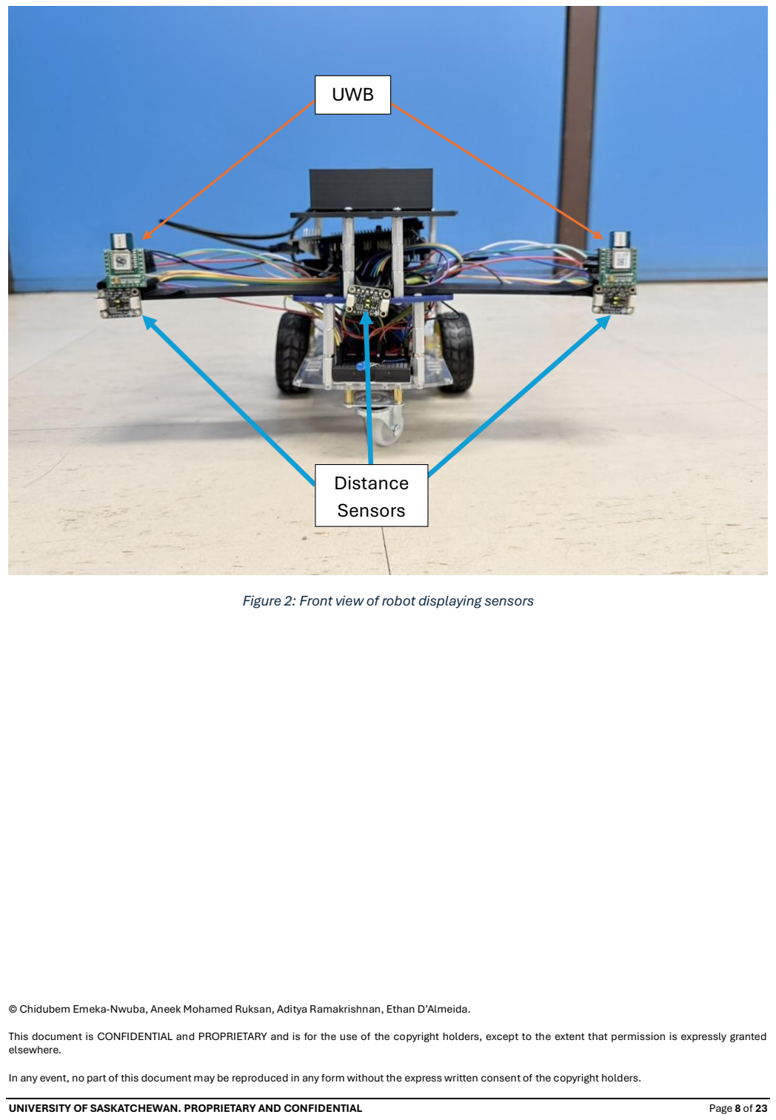
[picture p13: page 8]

© Chidubem Emeka-Nwuba, Aneek Mohamed Ruksan, Aditya Ramakrishnan, Ethan D’Almeida.

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

UNIVERSITY OF SASKATCHEWAN. PROPRIETARY AND CONFIDENTIAL | Page 8 of 23

Figure 2: Front view of robot displaying sensors

UWB

Distance
Sensors

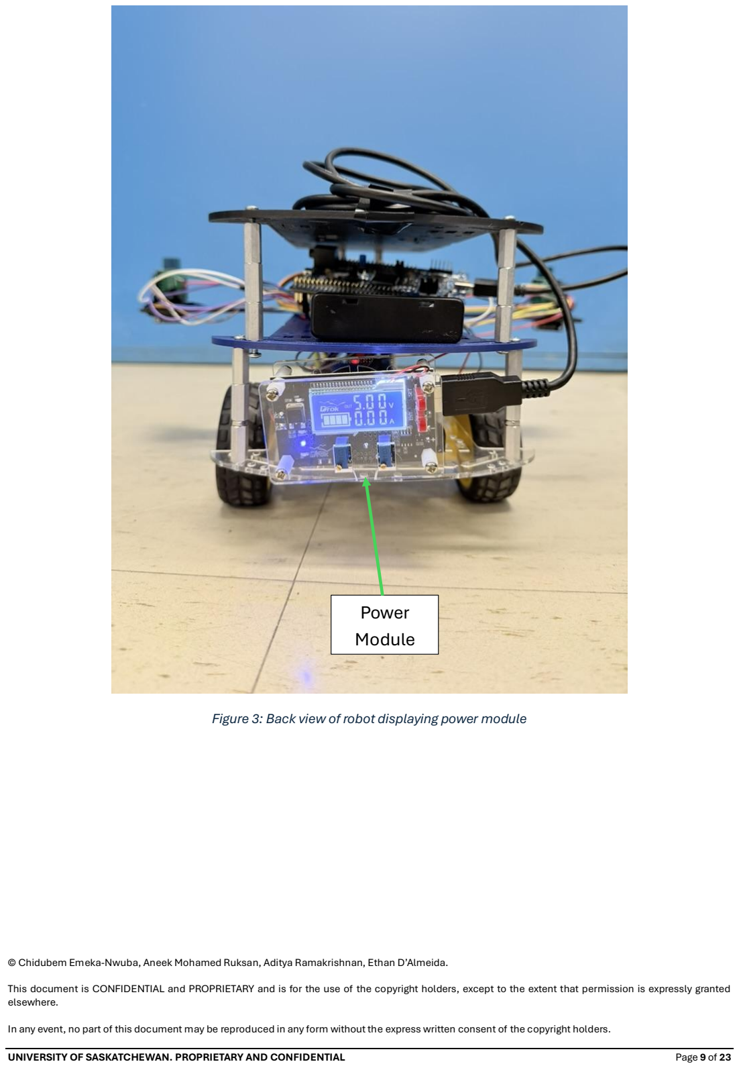
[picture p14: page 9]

© Chidubem Emeka-Nwuba, Aneek Mohamed Ruksan, Aditya Ramakrishnan, Ethan D’Almeida.

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

UNIVERSITY OF SASKATCHEWAN. PROPRIETARY AND CONFIDENTIAL | Page 9 of 23

Figure 3: Back view of robot displaying power module

Power
Module

© Chidubem Emeka-Nwuba, Aneek Mohamed Ruksan, Aditya Ramakrishnan, Ethan D’Almeida.

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

UNIVERSITY OF SASKATCHEWAN. PROPRIETARY AND CONFIDENTIAL | Page 10 of 23

## Quick Start Guide

Use this section when you want the shortest path from setup to operation.

Step | Action | What you should do
1 | Inspect the robot | Confirm that the robot is clean, dry, fully assembled, and free of loose wires or obvious damage.
2 | Check battery charge | Make sure the battery is installed correctly and has enough charge for your session.
3 | Prepare your workspace | Clear loose obstacles from the floor and confirm that your intended route is open.
4 | Load your tools | Place tools securely on the platform so the load is balanced and does not hang over moving parts.
5 | Power on the robot | Follow procedures explained in the Powering On section
6 | Enable user tracking | Activate the tracking function by pressing the STANDBY toggle button on the User remote.
7 | Begin walking | Move forward smoothly and allow the robot to establish and maintain its following distance.
8 | Stop when finished | Bring the robot to a controlled stop by activating standby, and power it off, and recharge if needed.

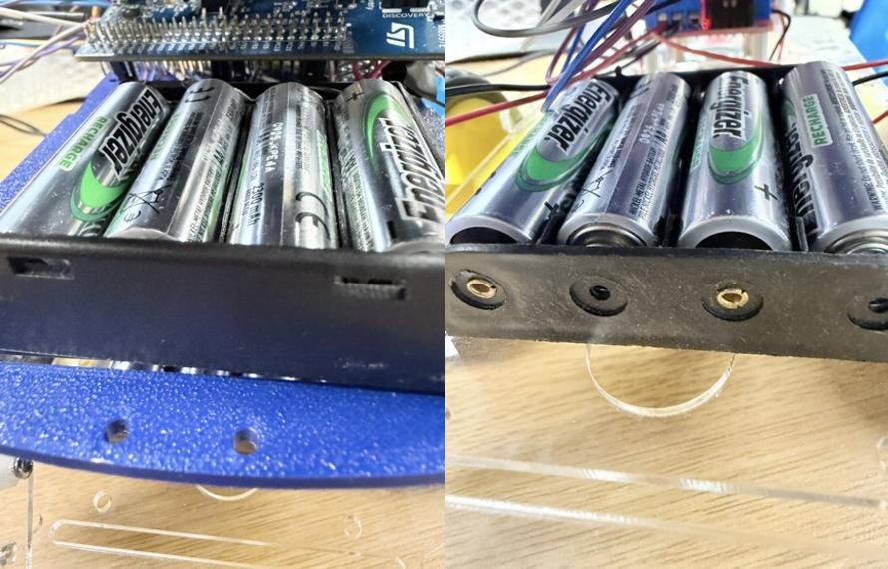
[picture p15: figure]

© Chidubem Emeka-Nwuba, Aneek Mohamed Ruksan, Aditya Ramakrishnan, Ethan D’Almeida.

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

UNIVERSITY OF SASKATCHEWAN. PROPRIETARY AND CONFIDENTIAL | Page 11 of 23

## Operating Your Robot

## Before you power on

Before each use, confirm that your battery is seated, your load is secure, your sensors are unobstructed, and the floor path is clear.

## Powering on

Step 1 - Install charged batteries
Insert fully charged rechargeable AA batteries into both battery holders:
- 4 AA batteries in the upper battery tray
- 4 AA batteries in the lower battery tray
Ensure correct polarity (+/–) before proceeding.

Figure 4: Upper and lower Battery tray with 4 rechargeable batteries each
Step 2 - Verify power module startup
After inserting the batteries, the power management module display will turn on.
- The display should show approximately 5.00 V output
- The charging indicator LED will be ON

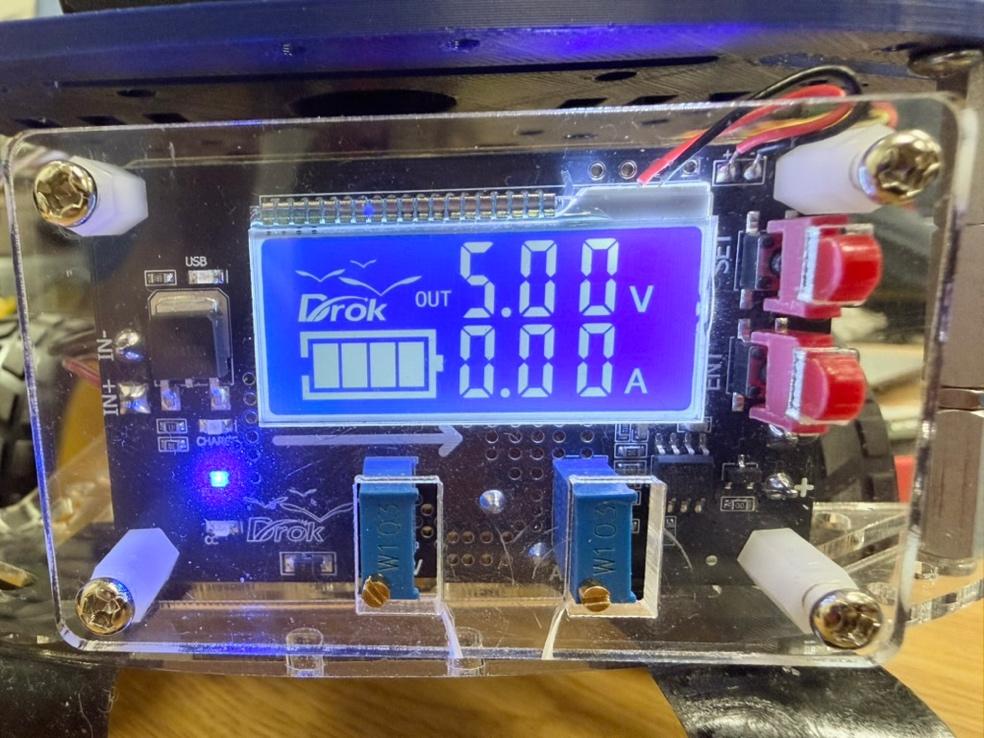
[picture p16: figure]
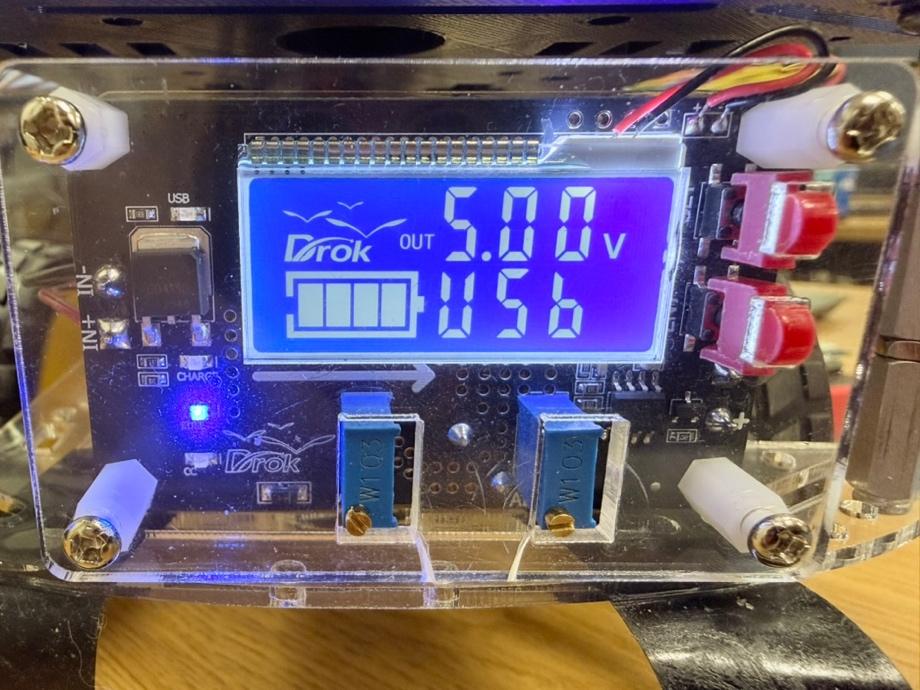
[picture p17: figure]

© Chidubem Emeka-Nwuba, Aneek Mohamed Ruksan, Aditya Ramakrishnan, Ethan D’Almeida.

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

UNIVERSITY OF SASKATCHEWAN. PROPRIETARY AND CONFIDENTIAL | Page 12 of 23

Figure 5: Power management module display after battery installation
Step 3 - Select USB output mode
Press the SET button (top red button) repeatedly until the display cycles to the USB output mode.

Figure 6: Cycling through power modes using the SET button to select USB output mode

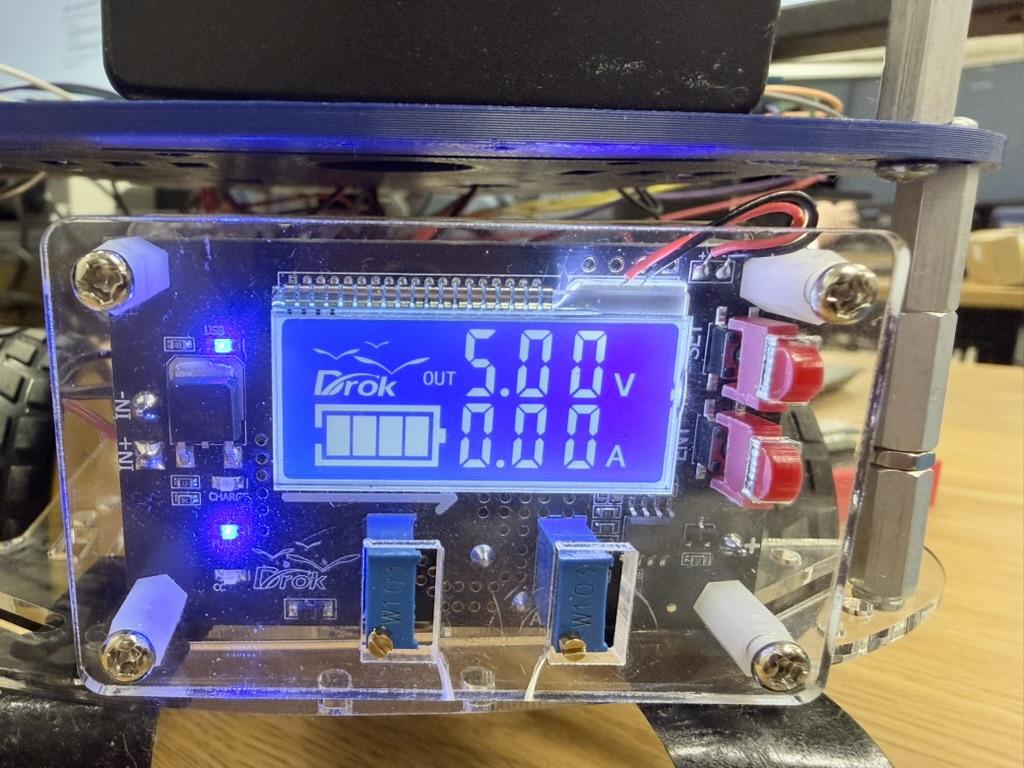
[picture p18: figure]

© Chidubem Emeka-Nwuba, Aneek Mohamed Ruksan, Aditya Ramakrishnan, Ethan D’Almeida.

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

UNIVERSITY OF SASKATCHEWAN. PROPRIETARY AND CONFIDENTIAL | Page 13 of 23
Step 4 - Enable output power
Press the ENT button (bottom red button) to enable power output.
- The USB indicator light will turn ON
- This confirms that the system is now supplying power

Figure 7: USB output enabled indicated by active current draw and USB indicator LED

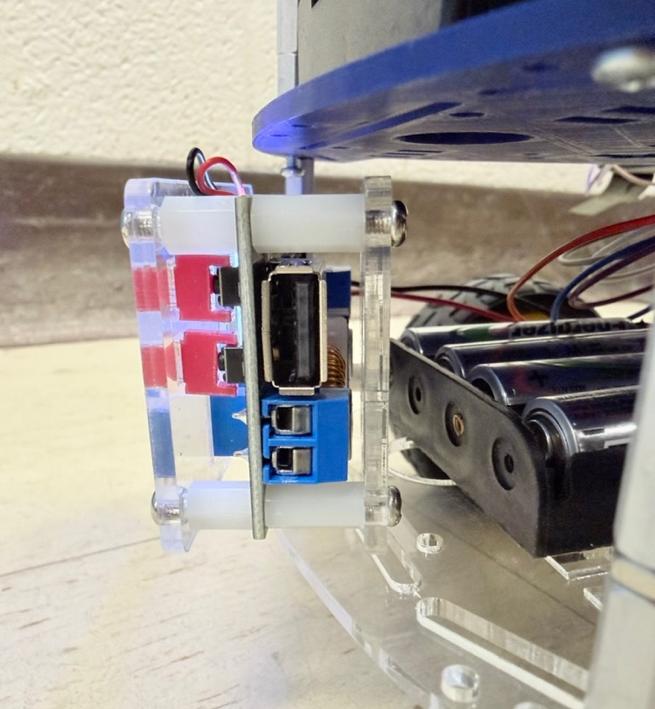
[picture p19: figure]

© Chidubem Emeka-Nwuba, Aneek Mohamed Ruksan, Aditya Ramakrishnan, Ethan D’Almeida.

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

UNIVERSITY OF SASKATCHEWAN. PROPRIETARY AND CONFIDENTIAL | Page 14 of 23
Step 5 - Connect system power cable
Insert the USB cable connected to the robot’s control board into the USB port on the power module.
- Once connected, the robot electronics will power up
- LEDs on the STM board and sensors should turn ON

Figure 8: Connecting USB cable from robot control board to the power module

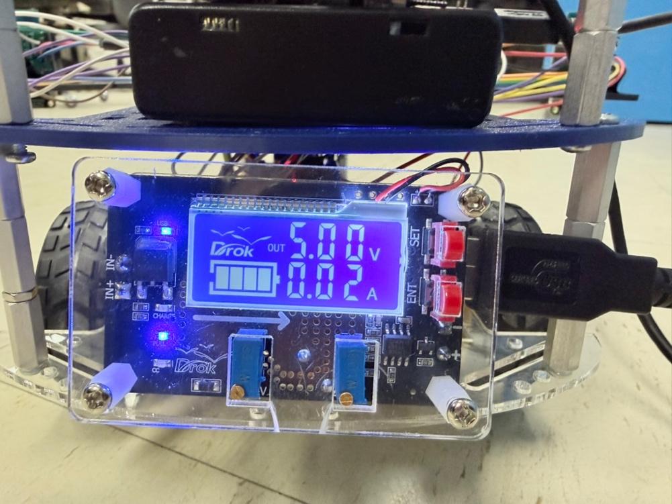
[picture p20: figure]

© Chidubem Emeka-Nwuba, Aneek Mohamed Ruksan, Aditya Ramakrishnan, Ethan D’Almeida.

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

UNIVERSITY OF SASKATCHEWAN. PROPRIETARY AND CONFIDENTIAL | Page 15 of 23
Step 6 - Confirm robot working
Verify the following before operation:
- Display shows stable voltage (~5V)
- Current draw is non-zero when system is active
- Controller and sensors are powered
The robot is now ready for operation.

Figure 9: Robot powered on with active voltage output and current draw displayed

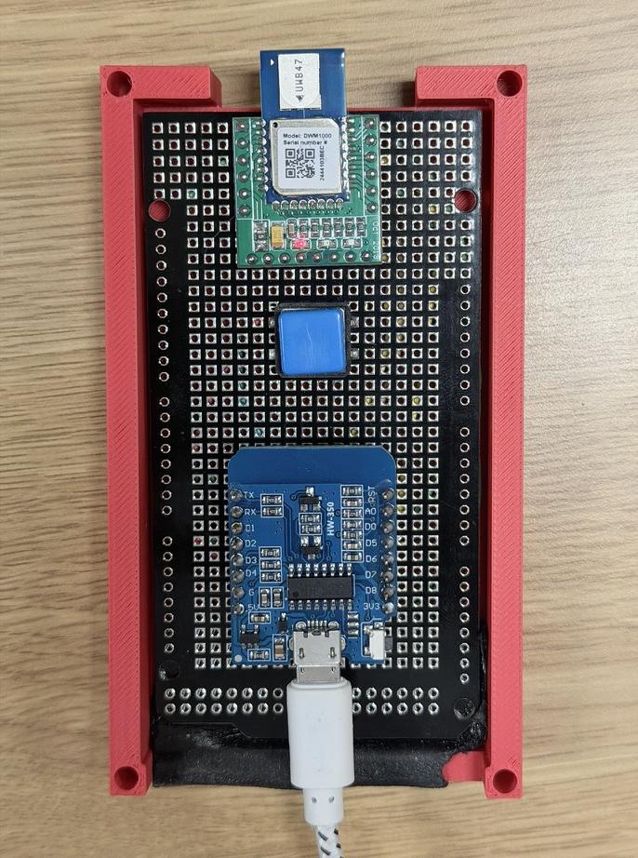
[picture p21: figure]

© Chidubem Emeka-Nwuba, Aneek Mohamed Ruksan, Aditya Ramakrishnan, Ethan D’Almeida.

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

UNIVERSITY OF SASKATCHEWAN. PROPRIETARY AND CONFIDENTIAL | Page 16 of 23
Step 7 - Power the User Remote
Connect a rechargeable power bank to the User remote using a Micro-B USB cable.
- Insert the Micro-B cable into the microcontroller board on the remote
- Connect the other end to the power bank
- Confirm the remote powers on (microcontroller LED active)
The User remote is now ready for tracking operation.

Figure 10: Connecting power to User remote using Micro-B USB cable

© Chidubem Emeka-Nwuba, Aneek Mohamed Ruksan, Aditya Ramakrishnan, Ethan D’Almeida.

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

UNIVERSITY OF SASKATCHEWAN. PROPRIETARY AND CONFIDENTIAL | Page 17 of 23

## Starting movement

The robot starts in standby mode by default.
To begin movement, position yourself within the robot’s tracking range and field of view:
- Stand anywhere within 30 meters of the robot
- Ensure you are within the forward 180° field of view (in front of the robot)
- Face the antenna generally toward the robot when initiating tracking
Press the STANDBY button on the User remote to disable standby mode and enable user tracking.
- The blue LED on the robot will turn OFF, indicating active tracking
- Begin walking at a steady, natural pace
- Allow a few seconds for the robot to acquire your position and stabilize Avoid sudden movement immediately after enabling tracking.

## During operation

During operation, remain within the robot’s tracking constraints:

- Stay within 30 meters of the robot
- Remain within the forward 180° field of view of the robot
- Avoid moving directly behind the robot without re-entering its front field of view Walk at a consistent pace and avoid abrupt changes:
- Take wider turns around obstacles or tight spaces
- Avoid sudden stops or rapid acceleration
- Periodically check behind to ensure proper following behavior
If the robot loses tracking or behaves unexpectedly, return to its front field of view and allow it to reacquire your position.

© Chidubem Emeka-Nwuba, Aneek Mohamed Ruksan, Aditya Ramakrishnan, Ethan D’Almeida.

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

UNIVERSITY OF SASKATCHEWAN. PROPRIETARY AND CONFIDENTIAL | Page 18 of 23

## Stopping the robot (Standby Mode)

To stop movement, place the robot into standby mode.
Press the STANDBY button on the User remote:
- The blue LED on the robot will turn ON, indicating standby mode
- The robot will immediately stop movement
While in standby mode:
- The robot remains powered
- Motors are disabled
- Pressing the STANDBY button again will resume tracking Use standby mode whenever:
- You need to pause operation
- The robot behaves unexpectedly
- You are adjusting payload or sensors

## Powering off

To fully power off the robot, disable power output from the power module.
1. Ensure the robot is in standby mode
2. Press the SET button until the display returns to the USB output setting
3. Press the ENT button to disable output - The USB indicator LED will turn OFF
4. Confirm the display remains active but output is disabled
5. Remove the batteries if required for storage or charging
The robot is now fully powered off.

Recommended operating habits

- Keep your load centered and as low as practical.
- Avoid sudden sprints, sharp pivots, or dragging the robot by hand while powered.
- Enable standby mode before adjusting wires, sensors, or the payload.
- Enable standby mode any time the robot does not respond the way you expect

© Chidubem Emeka-Nwuba, Aneek Mohamed Ruksan, Aditya Ramakrishnan, Ethan D’Almeida.

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

UNIVERSITY OF SASKATCHEWAN. PROPRIETARY AND CONFIDENTIAL | Page 19 of 23

## Charging and Battery Care

Charge the robot after each use or whenever the battery level is too low for reliable operation. Always ensure the robot is fully powered off before removing or installing batteries.
The robot is powered using eight (8) rechargeable AA batteries, which must be removed and charged using an external battery charger.
Use only rechargeable AA batteries (NiMH recommended) and a compatible charger. Handle batteries carefully during removal and installation to avoid damage to contacts or wiring.
The User remote is powered by a rechargeable power bank and should be charged separately as required.

## Charging procedure

1. Place the robot in standby mode, then follow the powering off procedure to fully power it off.
2. Remove all 8 AA rechargeable batteries from the robot.
3. Insert the batteries into the charger, ensuring correct polarity (+/–)
4. Connect the charger to a power source
5. Confirm charging using the charger’s indicator lights
6. Disconnect the User remote’s power bank from the remote
7. Connect the power bank to a suitable USB Type-C charger and confirm charging
8. Wait until both the batteries and power bank are fully charged
9. Disconnect all chargers and inspect cables and connectors before next use 10.Reinstall the batteries into the robot before operation

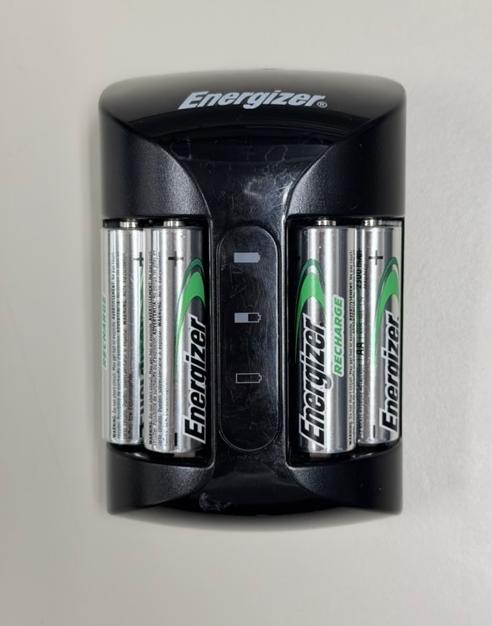
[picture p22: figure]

© Chidubem Emeka-Nwuba, Aneek Mohamed Ruksan, Aditya Ramakrishnan, Ethan D’Almeida.

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

UNIVERSITY OF SASKATCHEWAN. PROPRIETARY AND CONFIDENTIAL | Page 20 of 23

Figure 11: AA rechargeable batteries placed in charger

## Battery care guidelines

- Recharge the battery before it remains fully depleted for extended periods.
- Do not charge a battery that is visibly swollen, leaking, cracked, or overheated.
- Keep battery contacts clean and dry.
- Store batteries in a cool, dry indoor location when not in use.
- Record typical run time so you can spot battery health changes early.

© Chidubem Emeka-Nwuba, Aneek Mohamed Ruksan, Aditya Ramakrishnan, Ethan D’Almeida.

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

UNIVERSITY OF SASKATCHEWAN. PROPRIETARY AND CONFIDENTIAL | Page 21 of 23

## Routine Maintenance

Routine maintenance keeps your robot reliable, easier to troubleshoot, and safer to operate.

Task | Recommended frequency | What to check
Dust exterior surfaces | After each use | Remove dust and debris from the frame, tray, and exposed surfaces.
Inspect sensors | Before each use | Confirm sensors are clean and not blocked.
Check wheels and tires | Weekly | Look for debris, looseness, uneven wear, or reduced free rotation.
Inspect wiring and connectors | Weekly | Look for loose plugs, exposed conductors, pinched cables, or strain damage.
Check fasteners and mounts | Weekly | Make sure brackets, sensor mounts, and structural fasteners remain tight.
Review battery and charger condition | Weekly | Look for damage, overheating marks, or poor charge behavior.
Functional follow test | Before demonstrations | Confirm stable startup, tracking, stopping, and obstacle response.

## Storage and Transport

Store your robot indoors in a clean, dry location where it will not be struck by carts, tools, or foot traffic.
Turn the robot off before storage. Recharge the batteries and power bank if the robot will not be used for an extended period.
When transporting the robot, secure it so the frame, sensors, and wheels do not shift or impact other objects. Remove or secure loose tools before moving it.

© Chidubem Emeka-Nwuba, Aneek Mohamed Ruksan, Aditya Ramakrishnan, Ethan D’Almeida.

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

UNIVERSITY OF SASKATCHEWAN. PROPRIETARY AND CONFIDENTIAL | Page 22 of 23

## Troubleshooting

Use the table below to diagnose common problems.

Problem | Possible cause | What you should do
Robot will not power on | Battery discharged, battery disconnected, switch off, or loose wiring | Recharge the battery, confirm all power connections, and verify that the power module is on.
Robot powers on but does not move | Tracking not enabled, start sequence incomplete, or control fault | Confirm your tracking device is active, restart the robot, and repeat the normal startup sequence.
Robot does not follow smoothly | Sensor view blocked, user position unstable, floor clutter, or uneven load | Clean the sensors, walk at a steady pace, clear the path, and rebalance the payload.
Robot stops frequently | Obstacle detection is triggered or battery is low | Check for nearby obstacles, confirm sensor cleanliness, and recharge the battery if needed.
Movement is erratic | Loose hardware, slipping wheel, control issue, or unstable sensor reading | Stop operation immediately, inspect wheels and mounts, power cycle the robot, and do a short empty-load test.
Charging does not begin | Bad charger connection, charger fault, or damaged battery | Confirm the charger is fully connected, inspect the cable and connector, and do not continue if the battery shows damage.

If a fault remains after basic checks, stop using the robot and refer the issue to the project team or a supervisor.

© Chidubem Emeka-Nwuba, Aneek Mohamed Ruksan, Aditya Ramakrishnan, Ethan D’Almeida.

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

UNIVERSITY OF SASKATCHEWAN. PROPRIETARY AND CONFIDENTIAL | Page 23 of 23

## Technical Specifications

Overall dimensions | 20 x 32 x 18cm
Robot weight | 780g
Maximum payload | 1kg
Battery type | Rechargeable AA NiMH batteries (1.2V)
Typical runtime | 2.5 hours
Charging time | 5-7 hours
Recommended operating environment | Indoor, dry, level workspace

## Technical Support

Project support contact: Project team - lqv849@usask.ca , age159@usask.ca, szj128@usask.ca , cye810@usask.ca

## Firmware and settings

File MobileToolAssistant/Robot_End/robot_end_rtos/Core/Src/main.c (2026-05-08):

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
/* Includes ------------------------------------------------------------------*/
#include "main.h"
#include "cmsis_os.h"
#include "usb_host.h"

/* USER CODE BEGIN Includes */
#include "VL53L1X_api.h"
#include "VL53l1X_calibration.h"
#include "motor_hw.h"
#include "obst_det.h"
#include "dwm_triangulation.h"
#include "dwm1000.h"
/* USER CODE END Includes */

I2C_HandleTypeDef hi2c1;

I2S_HandleTypeDef hi2s3;

SPI_HandleTypeDef hspi1;

TIM_HandleTypeDef htim3;
TIM_HandleTypeDef htim12;

UART_HandleTypeDef huart3;

/* Definitions for Motor_Task */
osThreadId_t Motor_TaskHandle;
const osThreadAttr_t Motor_Task_attributes = {
  .name = "Motor_Task",
  .stack_size = 1024 * 4,
  .priority = (osPriority_t) osPriorityNormal,
};
/* Definitions for ObstDet_Task */
osThreadId_t ObstDet_TaskHandle;
const osThreadAttr_t ObstDet_Task_attributes = {
  .name = "ObstDet_Task",
  .stack_size = 1024 * 4,
  .priority = (osPriority_t) osPriorityAboveNormal,
};
/* Definitions for TrackUser_Task */
osThreadId_t TrackUser_TaskHandle;
const osThreadAttr_t TrackUser_Task_attributes = {
  .name = "TrackUser_Task",
  .stack_size = 1024 * 4,
  .priority = (osPriority_t) osPriorityHigh,
};
/* USER CODE BEGIN PV */

#define VL53_ADDR   (0x29 << 1)   // 0x52

uint16_t count = 0;

RemotePosition remote_pos = {
	.valid = 0
};

bool standby;


uint8_t device_id_1[4] = {0};
uint8_t device_id_2[4] = {0};

/* USER CODE END PV */

void SystemClock_Config(void);
static void MX_GPIO_Init(void);
static void MX_I2C1_Init(void);
static void MX_I2S3_Init(void);
static void MX_SPI1_Init(void);
static void MX_USART3_UART_Init(void);
static void MX_TIM3_Init(void);
static void MX_TIM12_Init(void);
void Start_MotorTask(void *argument);
void Start_ObstDet_Task(void *argument);
void Start_TrackUser_Task(void *argument);

/**
  * @brief  The application entry point.
  * @retval int
  */
int main(void)
{

  /* MCU Configuration--------------------------------------------------------*/

  /* Reset of all peripherals, Initializes the Flash interface and the Systick. */
  HAL_Init();

  /* Configure the system clock */
  SystemClock_Config();

  /* Initialize all configured peripherals */
  MX_GPIO_Init();
  MX_I2C1_Init();
  MX_I2S3_Init();
  MX_SPI1_Init();
  MX_USART3_UART_Init();
  MX_TIM3_Init();
  MX_TIM12_Init();
  /* Init scheduler */
  osKernelInitialize();

  /* USER CODE BEGIN RTOS_MUTEX */
  /* add mutexes, ... */
  /* USER CODE END RTOS_MUTEX */

  /* USER CODE BEGIN RTOS_SEMAPHORES */
  /* add semaphores, ... */
  /* USER CODE END RTOS_SEMAPHORES */

  /* USER CODE BEGIN RTOS_TIMERS */
  /* start timers, add new ones, ... */
  /* USER CODE END RTOS_TIMERS */

  /* USER CODE BEGIN RTOS_QUEUES */
  /* add queues, ... */
  /* USER CODE END RTOS_QUEUES */

  /* Create the thread(s) */
  /* creation of Motor_Task */
  Motor_TaskHandle = osThreadNew(Start_MotorTask, NULL, &Motor_Task_attributes);

  /* creation of ObstDet_Task */
  ObstDet_TaskHandle = osThreadNew(Start_ObstDet_Task, NULL, &ObstDet_Task_attributes);

  /* creation of TrackUser_Task */
  TrackUser_TaskHandle = osThreadNew(Start_TrackUser_Task, NULL, &TrackUser_Task_attributes);

  /* USER CODE BEGIN RTOS_THREADS */
  /* add threads, ... */
  /* USER CODE END RTOS_THREADS */

  /* USER CODE BEGIN RTOS_EVENTS */
  /* add events, ... */
  /* USER CODE END RTOS_EVENTS */

  /* Start scheduler */
  osKernelStart();

  /* We should never get here as control is now taken by the scheduler */

  /* Infinite loop */
  /* USER CODE BEGIN WHILE */
  while (1)
  {
    /* USER CODE END WHILE */

    /* USER CODE BEGIN 3 */
  }
  /* USER CODE END 3 */
}

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
/* USER CODE BEGIN Header_Start_MotorTask */
/**
  * @brief  Function implementing the Motor_Task thread.
  * @param  argument: Not used
  * @retval None
  */
/* USER CODE END Header_Start_MotorTask */
void Start_MotorTask(void *argument)
{
  /* init code for USB_HOST */
  /* USER CODE BEGIN 5 */
  MX_USB_HOST_Init();
  MotorHW_Init();

  for(;;)
  {
      MotorHW_TaskStep();
      count++;
      osDelay(20);
  }
  /* USER CODE END 5 */
}

/* USER CODE BEGIN Header_Start_ObstDet_Task */
/**
* @brief Function implementing the ObstDet_Task thread.
* @param argument: Not used
* @retval None
*/
/* USER CODE END Header_Start_ObstDet_Task */
void Start_ObstDet_Task(void *argument)
{
  /* USER CODE BEGIN Start_ObstDet_Task */
	int status;

	/* Reset sensor data */
	for(int i = 0; i < TOF_SENSOR_COUNT; i++)
		ToF_ResetData(&ToF_DATA[i]);

	/* Assign I2C addresses */
	ToF_AssignAddresses();

	/* Initialize sensors */
	for(int i = 0; i < TOF_SENSOR_COUNT; i++)
		status = ToF_InitSensor(tofAddresses[i], &ToF_DATA[i]);
  /* Infinite loop */
	for(;;)
	{
		ToF_UpdateSensors();
		osDelay(20);
	}
  /* USER CODE END Start_ObstDet_Task */
}

/* USER CODE BEGIN Header_Start_TrackUser_Task */
/**
* @brief Function implementing the TrackUser_Task thread.
* @param argument: Not used
* @retval None
*/
/* USER CODE END Header_Start_TrackUser_Task */
void Start_TrackUser_Task(void *argument)
{
  /* USER CODE BEGIN Start_TrackUser_Task */
//	RemotePosition remote_pos = {
//				.valid = 0
//		};
//
//		bool standby;

	DWM_Triangulation_Init(&hspi1);
  /* Infinite loop */
	for(;;)
	  {
		  DWM_Triangulation_TaskStep();

		  DWM_Triangulation_GetPosition(&remote_pos);
		  standby = get_standby_state();

		osDelay(10);
	  }
  /* USER CODE END Start_TrackUser_Task */
}

/**
  * @brief  Period elapsed callback in non blocking mode
  * @note   This function is called  when TIM1 interrupt took place, inside
  * HAL_TIM_IRQHandler(). It makes a direct call to HAL_IncTick() to increment
  * a global variable "uwTick" used as application time base.
  * @param  htim : TIM handle
  * @retval None
  */
void HAL_TIM_PeriodElapsedCallback(TIM_HandleTypeDef *htim)
{
  if (htim->Instance == TIM1)
  {
    HAL_IncTick();
  }
}

/**
  * @brief  This function is executed in case of error occurrence.
  * @retval None
  */
void Error_Handler(void)
{
  /* USER CODE BEGIN Error_Handler_Debug */
  /* User can add his own implementation to report the HAL error return state */
  __disable_irq();
  while (1)
  {
  }
  /* USER CODE END Error_Handler_Debug */
}
#ifdef USE_FULL_ASSERT
/**
  * @brief  Reports the name of the source file and the source line number
  *         where the assert_param error has occurred.
  * @param  file: pointer to the source file name
  * @param  line: assert_param error line source number
  * @retval None
  */
void assert_failed(uint8_t *file, uint32_t line)
{
  /* USER CODE BEGIN 6 */
  /* User can add his own implementation to report the file name and line number,
     ex: printf("Wrong parameters value: file %s on line %d\r\n", file, line) */
  /* USER CODE END 6 */
}
#endif /* USE_FULL_ASSERT */

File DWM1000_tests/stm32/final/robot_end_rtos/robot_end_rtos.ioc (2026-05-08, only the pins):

Mcu.UserName=STM32F407VGTx
PA0-WKUP.GPIO_Label=B1 [Blue PushButton]
PA0-WKUP.Signal=GPXTI0
PA1.GPIO_Label=DWM2_RESET_N
PA1.Signal=GPIO_Output
PA10.GPIO_Label=OTG_FS_ID
PA10.Signal=USB_OTG_FS_ID
PA11.GPIO_Label=OTG_FS_DM
PA11.Signal=USB_OTG_FS_DM
PA12.GPIO_Label=OTG_FS_DP
PA12.Signal=USB_OTG_FS_DP
PA13.GPIO_Label=SWDIO
PA13.Signal=SYS_JTMS-SWDIO
PA14.GPIO_Label=SWCLK
PA14.Signal=SYS_JTCK-SWCLK
PA2.GPIO_Label=DWM1_RESET_N
PA2.Signal=GPIO_Output
PA3.GPIO_Label=DWM3_RESET_N
PA3.Signal=GPIO_Output
PA4.GPIO_Label=I2S3_WS [CS43L22_LRCK]
PA4.Signal=I2S3_WS
PA5.GPIO_Label=SPI1_SCK
PA5.Signal=SPI1_SCK
PA6.GPIO_Label=SPI1_MISO
PA6.Signal=SPI1_MISO
PA7.GPIO_Label=SPI1_MOSI
PA7.Signal=SPI1_MOSI
PA9.GPIO_Label=VBUS_FS
PA9.Signal=USB_OTG_FS_VBUS
PB0.GPIO_Label=DWM3_CS_N
PB0.Signal=GPIO_Output
PB10.GPIO_Label=CLK_IN [MP45DT02_CLK]
PB10.Signal=I2S2_CK
PB11.Signal=USART3_RX
PB2.GPIO_Label=BOOT1
PB2.Signal=GPIO_Input
PB3.GPIO_Label=SWO
PB3.Signal=SYS_JTDO-SWO
PB4.GPIO_Label=Motor2 Fwd
PB4.Signal=S_TIM3_CH1
PB5.GPIO_Label=Motor2 Rev
PB5.Signal=S_TIM3_CH2
PB6.GPIO_Label=I2C1_SCL
PB6.Signal=I2C1_SCL
PB9.GPIO_Label=I2C1_SDA
PB9.Signal=I2C1_SDA
PC0.GPIO_Label=OTG_FS_PowerSwitchOn
PC0.Signal=GPIO_Output
PC10.GPIO_Label=I2S3_SCK [CS43L22_SCLK]
PC10.Signal=I2S3_CK
PC12.GPIO_Label=I2S3_SD [CS43L22_SDIN]
PC12.Signal=I2S3_SD
PC14-OSC32_IN.GPIO_Label=PC14-OSC32_IN
PC14-OSC32_IN.Signal=RCC_OSC32_IN
PC15-OSC32_OUT.GPIO_Label=PC15-OSC32_OUT
PC15-OSC32_OUT.Signal=RCC_OSC32_OUT
PC3.GPIO_Label=PDM_OUT [MP45DT02_DOUT]
PC3.Signal=I2S2_SD
PC4.GPIO_Label=DWM1_CS_N
PC4.Signal=GPIO_Output
PC5.GPIO_Label=DWM2_CS_N
PC5.Signal=GPIO_Output
PC7.GPIO_Label=I2S3_MCK [CS43L22_MCLK]
PC7.Signal=I2S3_MCK
PC8.GPIO_Label=Motor1 Rev
PC8.Signal=S_TIM3_CH3
PC9.GPIO_Label=Motor1 Fwd
PC9.Signal=S_TIM3_CH4
PD12.GPIO_Label=LD4 [Green Led]
PD12.Signal=GPIO_Output
PD13.GPIO_Label=LD3 [Orange Led]
PD13.Signal=GPIO_Output
PD14.GPIO_Label=LD5 [Red Led]
PD14.Signal=GPIO_Output
PD15.GPIO_Label=LD6 [Blue Led]
PD15.Signal=GPIO_Output
PD4.GPIO_Label=Audio_RST [CS43L22_RESET]
PD4.Signal=GPIO_Output
PD5.GPIO_Label=OTG_FS_OverCurrent
PD5.Signal=GPIO_Input
PD8.Signal=USART3_TX
PE1.GPIO_Label=MEMS_INT2 [LIS302DL_INT2]
PE1.Signal=GPXTI1
PE3.GPIO_Label=CS_I2C/SPI [LIS302DL_CS_I2C/SPI]
PE3.Signal=GPIO_Output
PH0-OSC_IN.GPIO_Label=PH0-OSC_IN
PH0-OSC_IN.Signal=RCC_OSC_IN
PH1-OSC_OUT.GPIO_Label=PH1-OSC_OUT
PH1-OSC_OUT.Signal=RCC_OSC_OUT

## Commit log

2026-05-08 added 3D printing chassis files
    [Case.stl, Chassis.stl, RobotArmStart v1.stl]
2026-05-08 added documentation files to docs/
    [Case.stl, Chassis.stl, RobotArmStart v1.stl]

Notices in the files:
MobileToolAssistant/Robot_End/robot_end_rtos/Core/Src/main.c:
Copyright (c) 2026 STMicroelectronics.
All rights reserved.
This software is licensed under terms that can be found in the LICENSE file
